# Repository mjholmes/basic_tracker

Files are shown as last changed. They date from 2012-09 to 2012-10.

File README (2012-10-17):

Basic tracker

The project is to create a simple tracking PCB that can be used for tracking high
altitude balloons. The project is designed to be easilly assembled from off the shelf
modules and easilly obtainable through hole soldered components. An arduino Pro mini
is used rather than designing the board to have an ATMega328 to reduct component count
and increase reliability.

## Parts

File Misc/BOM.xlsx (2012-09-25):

PCB ID | Description | Item | Supplier | Order code | Quantity | Unit Cost
 | Processor board | Arduino Pro mini 3.3v 8MHz | Cool components | 000176 | 1 | 15 | 15
ARDUINO_MINI | Processor board connectors | 1x12 2.54mm pitch pin header | Farnell |  | 2 |  | 0
JP3 | 1-Wire ext sensor port | JST PH 3pin connector 2mm pitch | Farnell |  | 1 |  | 0
JP4 | Debug serial port | JST PH 3pin connector 2mm pitch | Farnell |  | 1 |  | 0
JP5 | AVR ICSP port | 2x3 2.54mm pitch pin header | Farnell |  | 1 |  | 0
JP1 | CSGSHOP GPS Port | 2x3 2.54mm pitch pin header | Farnell |  | 0 |  | 0
 | CSGSHOP GPS board | UBLOX MAX-6 reference board | CSGSHOP |  | 0 |  | 0
JP2 | HAB Supplies GPS port | 1x8 2.54mm pitch pin header | Farnell |  | 1 |  | 0
 | HAB Supplies GPS board | UBLOX MAX-6 breakout 3.3v | HAB supplies | HAB-BO-M6A | 1 | 29.99 | 29.99
DS1820 | Internal temperature sensor | Dallas DS18B20 TO92 package | Farnell | SC10426 | 1 | 2.98 | 2.98
 | External temperature sensor | Dallas DS18B20 TO92 package | Farnell | SC10426 | 1 | 2.98 | 2.98
R4 | 1-Wire pullup | MF25 series 4.7k 1/4 watt resistor | Farnell | 341951 | 1 | 0.02 | 0.02
NTX2 | Radio transmitter | Radiometrix NTX2 | HAB Supplies | HAB-NTX2-650 | 1 | 19.79 | 19.79
R8, R9 | Voltage divider resistors | MF25 series 4.7k 1/4 watt resistor | Farnell | 341951 | 2 | 0 | 0
R7 | Voltage divider bias resistors | MF25 series 30k 1/4 watt resistor | Farnell | RE05318 | 1 | 0.02 | 0.02
R1 | LED current limiting resistor | MF25 series 820R 1/4 watt resistor | Farnell | RE04991 | 1 | 0.38 | 0.38
LED1 | Status LED | Green 3mm LED | Farnell | 1003209 | 1 | 0.1 | 0.1
IC1 | Voltage regulator | Microchip MCP1700 3.3v LDO | Farnell | SC08304 | 1 | 0.25 | 0.25
C1 | LDO capacitor | 1000nF ceramic | Farnell | 121-6447 | 1 | 1 | 1
C2 | LDO capacitor | 1000nF ceramic | Farnell | 121-6447 | 1 | 1 | 1
CN1 | Battery connector | JST PH 2pin connector 2mm pitch | Farnell |  | 1 |  | 0
R5 | Voltage divider, battery mon | MF25 series 22k 1/4 watt resistor | Farnell | RE03743 | 1 | 0.38 | 0.38
R6 | Voltage divider, battery mon | MF25 series 22k 1/4 watt resistor | Farnell | RE03743 | 1 | 0 | 0
X1 | SMA Jack | Right angle SMA jack | HAB supplies | HAB-SMAPCB | 1 | 2.4 | 2.4
 |  |  |  |  | Total cost |  | 76.29

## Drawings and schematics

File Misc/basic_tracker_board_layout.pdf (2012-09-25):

## Radiometrix NTX2

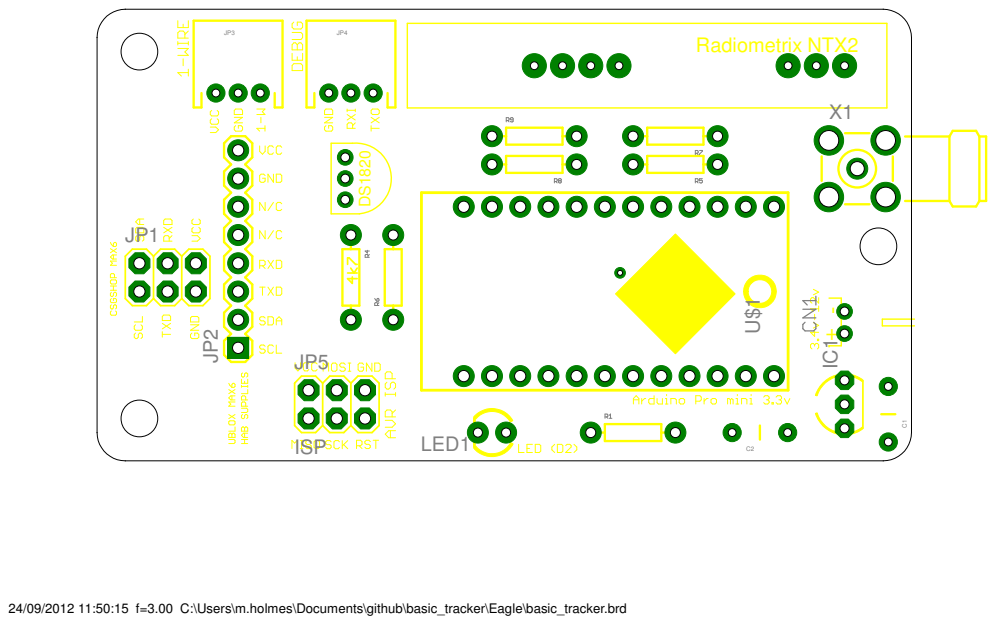
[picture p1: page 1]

24/09/2012 11:50:15 f=3.00 C:\Users\m.holmes\Documents\github\basic_tracker\Eagle\basic_tracker.brd

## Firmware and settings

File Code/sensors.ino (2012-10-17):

// Initialise the ADC
void initBattSensor(void) {
  // Just in case it has been changed elsewhere
  analogReference(DEFAULT);
}

float getVBatt(void) {
  // Read the pin level. We'll discard this reading and then wait a little to make sure
  // that the multiplexer is on the right pin and the S/H caps have had time to charge.
  int vBatt = analogRead(VBATT_PIN);
  delay(5);
  
  // Now take the proper reading
  vBatt = analogRead(VBATT_PIN);
  if (DEBUG) {
    DBG_PORT.print("VBatt raw: ");
    DBG_PORT.println(vBatt, DEC);
  }
  return (float) vBatt * 0.00322 * VBATT_ADC_CAL;
}








// Initialuse and configure the dallas devices
void initDallasSensors(void) {
   // Start up the library
  sensors.begin();
  
  if (sensors.isParasitePowerMode()) DBG_PORT.println("1wire parasite on!");
  
  // locate devices on the bus
  unsigned int numSensors = sensors.getDeviceCount();
  if (DEBUG) {
    DBG_PORT.print("Found ");
    DBG_PORT.print(numSensors, DEC);
    DBG_PORT.println(" 1wire devs.");
  }
 
  // See how many sensors we've got and initialise them
  if (numSensors > 0) {
    // At least one sensor was found
    if (sensors.isConnected(intThermometer)) {
      // We've found our internal sensor
      if (DEBUG) {
        DBG_PORT.print("Int tsens found");
        DBG_PORT.println();
      }
    
      // Set resolution
      sensors.setResolution(intThermometer, TEMPERATURE_PRECISION);
        
      // Verify resolution
      unsigned int resolution = sensors.getResolution(intThermometer);
      if (resolution != TEMPERATURE_PRECISION) {
        DBG_PORT.print("Int tsens precis failed");
      }
      else DBG_PORT.println("Int tsens precis set");
    }
    else DBG_PORT.println("Int tsens not found");


    if (sensors.isConnected(extThermometer)) {
      // We've found our external sensor
      if (DEBUG) {
        DBG_PORT.print("Ext tsens found");
        DBG_PORT.println();
      }
    
      // Set resolution
      sensors.setResolution(extThermometer, TEMPERATURE_PRECISION);
        
      // Verify resolution
      unsigned int resolution = sensors.getResolution(extThermometer);
      if (resolution != TEMPERATURE_PRECISION) {
        DBG_PORT.print("Ext tsens precis failed");
      }
      else DBG_PORT.println("Ext tsens precis set");
    }
    else DBG_PORT.println("Ext tsens not found");
 
  }
  else {
    DBG_PORT.println("No tsens found");
  }

}

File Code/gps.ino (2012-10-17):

// GPS functions


// Sync chars that are at the start of each string
const byte uBloxSync1 = 0xB5;
const byte uBloxSync2 = 0x62;


void initGPS(void) {
  // Set airbourne mode
  setNav5();

  // Switch off periodic NMEA sentences, we'll poll the module when
  // we want some information. 40 is message ID, GGA/GLL/etc is the NMEA
  // sentence to change. The first 5 0s relate to an output port. On the u-blox max-6
  // the ports are ddc, usart1, usart2, usb and spi. The last 0 is reserved.
  // See UBLOX protocol spec section 21.11 (page 80).
  GPS_PORT.println("$PUBX,40,GGA,0,0,0,0,0,0*5A");  // MJH changed these from GGA,0,0,0,0*5A ie added 2 more 0s
  GPS_PORT.println("$PUBX,40,GLL,0,0,0,0,0,0*5C");
  GPS_PORT.println("$PUBX,40,GSA,0,0,0,0,0,0*4E");
  GPS_PORT.println("$PUBX,40,GSV,0,0,0,0,0,0*59");
  GPS_PORT.println("$PUBX,40,RMC,0,0,0,0,0,0*47");
  GPS_PORT.println("$PUBX,40,VTG,0,0,0,0,0,0*5E");

  // Allow the GPS time to process the requests
  delay(1000); // CHECK THIS TIMING WITH DATASHEET
  
  // Delete anything that might still be in the GPS Rx buffer
  clearGPSBuffer();
}
  
void setNav5(void) {
  // Make sure the GPS is in airbourne mode. See u-blox protocol spec
  // section 31.10.2 for details of the CFG-NAV5 command and section 24
  // (page 82) for UBX packet structure. u-center binary console can be
  // used to sniff this data rather than having to work it all out.
  uint8_t cfgNav5[] = {0xB5, 0x62, 0x06, 0x24,                // Sync chars mu and b plus class and id values
                       0x24, 0x00,                            // Length of data (in bytes, little endian) - 36dec
                       0xFF, 0xFF, 0x06, 0x03, 0x00, 0x00,    // Data
                       0x00, 0x00, 0x10, 0x27, 0x00, 0x00,
                       0x05, 0x00, 0xFA, 0x00, 0xFA, 0x00,
                       0x64, 0x00, 0x2C, 0x01, 0x00, 0x00,
                       0x00, 0x00, 0x00, 0x00, 0x00, 0x00,
                       0x00, 0x00, 0x00, 0x00, 0x00, 0x00,
                       0x16, 0xDC};                           // 16bit Checksum, 8bit Fletcher (RFC1146) calculated
                                                              // over class, id, length and data (not sync chars).
                      
  sendUBX(cfgNav5, sizeof(cfgNav5)/sizeof(uint8_t));
}


// Return the status of the GPS
boolean gpsLock(void) {
}

// Poll the GPS for UBX proprietary message. See UBLOX protocol spec section 21.1 (page 66)
void pollGPS(void) {
  GPS_PORT.println("$PUBX,00*33");
}

// Print some status on valid data received by TinyGPS
void gpsPrintStats() {
  unsigned long chars = 0;
  unsigned short good_sentences = 0, failed_cs = 0;
  gps.stats(&chars, &good_sentences, &failed_cs);
  #ifdef DEBUG
    DBG_PORT.print("TinyGPS Stats - ");
    DBG_PORT.print(chars, DEC);
    DBG_PORT.print("chars, ");
    DBG_PORT.print(good_sentences, DEC);
    DBG_PORT.print("good, ");
    DBG_PORT.print(failed_cs, DEC);
    DBG_PORT.println("failed cs.");
  #endif
}

// THIS IS NOT RIGHT
void gpsChecksum(byte *buffer) {
  byte CK_A = 0, CK_B = 0;
  for(int i=0;i<sizeof(&buffer)/sizeof(byte);i++) {
    CK_A = CK_A + buffer[i];
    CK_B = CK_B + CK_A;
  }
}

// Send a byte array of UBX protocol to the GPS
void sendUBX(uint8_t *MSG, uint8_t len) {
  for(int i=0; i<len; i++) {
    GPS_PORT.write(MSG[i]);
  }
}

// Calculate expected UBX ACK packet and parse UBX response from GPS
boolean getUBX_ACK(uint8_t *MSG) {
  uint8_t b;
  uint8_t ackByteID = 0;
  uint8_t ackPacket[10];
  unsigned long startTime = millis();
  #ifdef DEBUG
  DBG_PORT.print(" * Reading ACK response: ");
  #endif
 
  // Construct the expected ACK packet    
  ackPacket[0] = 0xB5;	  // header
  ackPacket[1] = 0x62;	  // header
  ackPacket[2] = 0x05;	  // class
  ackPacket[3] = 0x01;	  // id
  ackPacket[4] = 0x02;	  // length
  ackPacket[5] = 0x00;
  ackPacket[6] = MSG[2];  // ACK class
  ackPacket[7] = MSG[3];  // ACK id
  ackPacket[8] = 0;       // Checksum
  ackPacket[9] = 0;
 
  // Calculate the checksums
  for (uint8_t i=2; i<8; i++) {
    ackPacket[8] = ackPacket[8] + ackPacket[i];
    ackPacket[9] = ackPacket[9] + ackPacket[8];
  }
 
  while (1) {
 
    // Test for success
    if (ackByteID > 9) {
      // All packets in order!
      #ifdef DEBUG
      DBG_PORT.println(" (SUCCESS!)");
      #endif
      return true;
    }
 
    // Timeout if no valid response in 3 seconds
    if (millis() - startTime > 3000) {
      #ifdef DEBUG
      DBG_PORT.println(" (FAILED!)");
      #endif
      return false;
    }
 
    // Make sure data is available to read
    if (GPS_PORT.available()) {
      b = GPS_PORT.read();
 
      // Check that bytes arrive in sequence as per expected ACK packet
      if (b == ackPacket[ackByteID]) { 
        ackByteID++;
        #ifdef DEBUG
        DBG_PORT.print(b, HEX);
        #endif
      } 
      else {
        ackByteID = 0;	// Reset and look again, invalid order
      }
 
    }
  }
}




// Function to poll the "dynamic platform model" being used by the Ublox GPS module
// Sends a UBX command (requires the function sendUBX()) and waits 3 seconds
// for a reply from the module. It then isolates the byte which contains 
// the information regarding current mode. Possible values are:
//   0 Portable
//   2 Stationary
//   3 Pedestrian 
//   4 Automotive
//   5 Sea
//   6 Airborne with <1g Acceleration
//   7 Airborne with <2g Acceleration
//   8 Airborne with <4g Acceleration
// A full decription of the above modes can be found in section 2.1 (page 1)
// of the uBLOX protocol spec
// Adapted by jcoxon from getUBX_ACK() from the example code on UKHAS wiki
// http://wiki.ukhas.org.uk/guides:falcom_fsa03

// PROBLEM - THIS DOESNT DO CHECKSUMS AND DOESNT VERIFY THAT THE START BYTES ARE CORRECT
// NEED TO ADD SOME ERROR CHECKING AND START BIT CHECKING
uint8_t getNAV5dynModel(){
  uint8_t b, bytePos = 0;
  // Empty cfg-NAV5 message,  see UBLOX protocol spec section 31.10.1 (page 116)
  uint8_t getNAV5[] = { 0xB5, 0x62, 0x06, 0x24, // Sync chars mu and b plus class and id values
                        0x00, 0x00,             // 0 length data
                        0x2A, 0x84 };           // Checksum

  clearGPSBuffer();
  unsigned long startTime = millis();
  sendUBX(getNAV5, sizeof(getNAV5)/sizeof(uint8_t));
  while (1) {
    // Make sure data is available to read
    if (GPS_PORT.available()) {
      b = GPS_PORT.read();
      // Dynamic platform model is 1 byte unsigned int at addr 8
      // Header(2), ID(2), Length(2), Mask(2), dynModel(1)
      if(bytePos == 8){
        return b;
      }
      bytePos++;
    }

    // Timeout if no valid response in 3 seconds
    if (millis() - startTime > 3000) {
      return 98;
    }
  }
}
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

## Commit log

2012-08-29 Updated board text and cap sizes
    [basic_tracker.brd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]
2012-08-29 New gerber files based on a nottingham.ac.uk pcbtrain CAM file
    [basic_tracker.gbl, basic_tracker.gbo, basic_tracker.gbs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]
2012-08-30 Added a slightly modified version of the CAM file, tweaked the board and rerouted a few traces by hand
    [basic_tracker.brd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]
2012-08-30 Modified the bottom silkscreen text to show pin connections
    [basic_tracker.brd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]
2012-08-31 Added NTX2 connections to bottom silkscreen
    [basic_tracker.brd]
2012-09-25 Added datasheets and BOM. Fixed issue with v1 PCB
    The v1 PCB had an error with the battery voltage monitor - it was eing
    fed by Vcc not Vbatt so could only monitor the regulator voltage. Bumped
    schematic version to 1.1, board not yet re-routed.
    [BOM.xlsx, NTX2_shift_calc.xlsx, basic_tracker.brd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]
